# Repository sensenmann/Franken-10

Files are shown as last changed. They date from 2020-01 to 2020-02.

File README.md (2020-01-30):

# Franken-10
**A CR-10 Dual-X-Carriage Mod**

This is my first public Open Source project, so please be kind with me. Also, english isn't my native language - please forgive me typos and grammatical mistakes :wink:

:bangbang::bangbang:
**This is an unstable work in progress!! Don't use it now, until you're willing to contribute to this project!!**
:bangbang::bangbang:

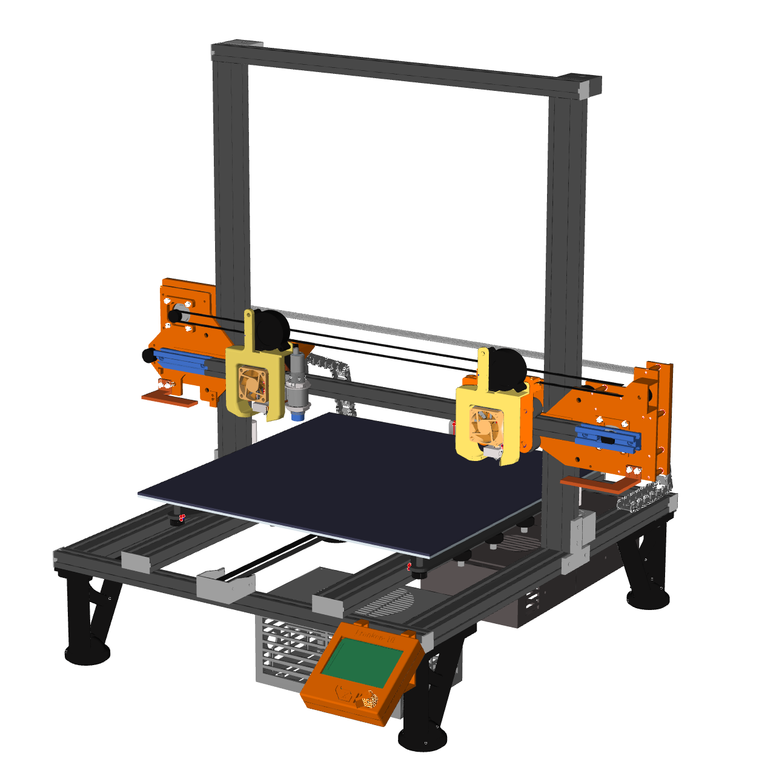
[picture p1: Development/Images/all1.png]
Franken-10


<h3>Table of Contents</h3>
<!-- TOC depthFrom:2 depthTo:6 withLinks:1 updateOnSave:1 orderedList:0 -->

- [Intention](#intention)
- [Benefits](#benefits)
- [Needed parts](#needed-parts)
- [Instructions](#instructions)
- [Firmware](#firmware)
- [FAQ](#faq)

<!-- /TOC -->

## Intention
I wanted to upgrade my awesome Creality CR-10 3D Printer to make it work with **dual X-Carriage** - but without building it completely up from the ground.
Also I want to keep the upgrades **cheap**, so everyone can easily join this journey.

At the moment, the overall costs for the needed parts is around **190€ - 320€**.

## Benefits
- TMC2130 upgrade
- Silent printing (thanks to TMC2130)
- Sensorless homing on X and Y
- Filament-Runout Sensor (by using existing endstops)
- 32 Bit Mainboard
- 2 independent extruders (fast switching)
- Autobedleveling and Mesh-Correction
- Basing on Marlin Firmware V2.0.1
- Using existing CR-10 Frame (no drilling, etc.)

## Needed parts
All needed and optionals parts can be found [here](Parts.md)

## Instructions
Do the CR-10 dual-z upgrade as instructed [here](https://www.sainsmart.com/blogs/news/how-to-install-dual-z-axis-to-upgrade-your-creality-cr-10-3d-printer).  
Skip the controlbox-steps and go directly to the step **Bracket installing**, as we have our own mainboard.

All other steps are documented in the **[manual](Docs)**  
:heavy_exclamation_mark: UNDER CONSTRUCTION :heavy_exclamation_mark:

## Firmware
You can find my fork of Marlin 2.0 [here](https://github.com/sensenmann/Franken-10-Marlin)   
The latest Firmware can be found in the **[releases](../../releases)**-section

## FAQ
Please also read the [FAQ](FAQ.md) - or ask questions by opening an Issue.

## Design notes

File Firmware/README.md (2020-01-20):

# Firmware Update Instructions

- Copy **firmware.bin** to the root of your MicroSD-Card
- Reset your SKR PRO board and wait till the update progress has finished

For further details look at the [original instructions](../../../blob/develop/Docs/3rd-Party/SKR%20PRO%20V1.1%20user%20manual%20v1.1.pdf).

# Build Marlin Firmware

To build the Marlin-Firmware please checkout [my fork](https://github.com/sensenmann/Franken-10-Marlin) of the original Marin-Firmware `bugfix-2.0.x`.

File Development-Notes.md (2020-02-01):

# Development-Notes
## 3D Models
All parts are designed in Fusion360 and located in the git-repository.  
I'm quiet new to Fusion360, so some models are maybe constructed a little bit "strange" in the eyes of experts 😅

At the moment, sensorless homing with `DUAL_X_CARRIAGE`enabled in Marlin wasn't possible for me, so I've had to make an workaround. You can find this fix in my commit **[150d5a9](https://github.com/sensenmann/Franken-10-Marlin/commit/150d5a96bf3c44fadcd32eb3756d982cddc0c70e)**.

I hope someone can help me to fix this workaround.

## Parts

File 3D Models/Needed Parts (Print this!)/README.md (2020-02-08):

# 3D Printing instructions

All parts are mechanical parts and should be printed in the **final version** with ABS/PETG and 100% infill.

For **developing/testing purpose** I've made very good experiences with PLA and 20% infill. This is stable enough! :grimacing:

## Franken-10 Parts

All parts can be printed without supports.  

### X-Holder Parts
- `X-Holder Left - Front.stl`
- `X-Holder Left - Back.stl`
- `X-Rails Extension - Left.stl`
- `X-Holder Right - Front.stl`
- `X-Holder Right - Back.stl`
- `X-Rails Extension - Right.stl`
- `Nozzle Wipe - Left.stl`
- `Nozzle Wipe - Right.stl`
- `M8 Rod Mount Left.stl`
- `M8 Rod Mount Right.stl`
- **18x** `Spacer.stl`
- `Endstopp-Part.stl` *(optional - only need, when you don't have an ABL-Probe)*

### Hotend Carriages
#### for E3D V6 Hotend - recommended
- `Carriage Left - E3DV6.stl`
- `Carriage Left - E3DV6 - Part 2.stl`
- `Carriage Left - E3DV6 - Part 2 - Cap.stl`
- `Carriage Right - E3DV6.stl`
- `Carriage Right - E3DV6 - Part 2.stl`
- `Carriage Right - E3DV6 - Part 2 - Cap.stl`
- `Carriage Right - E3DV6 - Part 2 - ABL.stl`
- **4x** `Nut-Holder.stl`
- **3x** `Exccentric Spacer.stl`

<div style="color: #BBBBBB">

#### for stock hotend *(not updated aynmore)*
- `Carriage Left - Stock Hotend.stl`
- `Carriage Left - Stock Hotend - Part 2.stl`
- `Carriage Left - Stock Hotend - Part 2 - Cap.stl`
- `Carriage Left - Stock Hotend - ABL.stl`
- `Carriage Right - Stock Hotend.stl`
- **3x** `Exccentric Spacer.stl`
</div>

### PSU + Mainboard Enclosures
- `PSU-Enclosure 1.stl`
- `PSU-Enclosure 2.stl`
- `PSU-Enclosure Cover 1.stl`
- `PSU-Enclosure Cover 2.stl`
- `SKR-Enclosure Bottom.stl`
- `SKR-Enclosure Cover.stl`
- `SKR-Enclosure Fan-Cover.stl`
- `SKR-Enclosure Walls.stl`

## 3rd Party Parts
### 5015 Bullseye Fans
Original part from https://www.thingiverse.com/thing:2759439
#### for E3D V6 Hotend - recommended
- **2x** `CR10_E3DV6_MANUAL_BASE_V7.5.stl`
- **2x** `E3DV6_DUCT_V7.5.stl`
- **2x** `E3DV6_OR_VOLC_40MM_CAP_V7.5.stl`

<div style="color: #BBBBBB">

#### for stock hotend *(not updated aynmore)*
- 2x `CR10_STOCK_MANUAL_BASE_V11.3.stl`
- 2x `CR10TEVO_5015_DUCT_V7.5....stl`
- Optional (for Autobed-Leveling):
  - `ALL_18MM_EZABL_X+48_Y-2_RIGHT_V7.5 - mirrored.stl` *(for 18mm Probes)*
  - `ALL_13MM_EZABL_X+48_Y-2_RIGHT_7.5..stl` *(for 13mm Probes)*
</div>

### CR-10 Feet
Original part from https://www.thingiverse.com/thing:3093788  
Print 4x `Pied-CR10-Update.STL` and mount it to the CR-10 frame.

## Filament-Runoutsensor Mount
Original part from http://www.thingiverse.com/thing:3352422  
Print 2x `Filament_Sensor_Crealityv1.stl`  
This part is using your existing CR-10 endstops.

### CR-10 Dual_Z Pulley-Setup
Original part from https://www.thingiverse.com/thing:2628377  
Print `Idle_Pulley_Tension_Bracket.stl`

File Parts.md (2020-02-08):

# Parts
## Needed Parts

| Pic | Name | Shoplink | Price (ca) |
|--|--|--|--|
|  | **CR-10 Dual Z Axis upgrade** | [Amazon](https://amzn.to/2GDkn1D) / [Aliexpress](https://www.aliexpress.com/item/33005235559.html)| 22€ - 45€  |
|  | **SKR Pro v1.1 Mainboard**<br>with 6 Steppermotor-Drivers | [Amazon](https://www.amazon.de/gp/product/B07W5XS572/) / [Aliexpress](https://www.aliexpress.com/item/33042699158.html) | 33€ - 50€ |
|  | **6x TMC2130 Steppermotor Drivers**<br>in SPI-Mode | [Amazon](https://amzn.to/3aTRr3j) / [Aliexpress](https://www.aliexpress.com/item/32907648703.html) | 50€ - 70€ |
|  | **RepRap Discount LCD 12864**<br>with SD-Card Slot | [Amazon](https://amzn.to/37FaMn7) / [Aliexpress](https://www.aliexpress.com/item/4000331136499.html) | 11€ - 16€ |
|  | **6x TMC2130 Steppermotor Drivers**<br>in SPI-Mode | [Amazon](https://amzn.to/2OblObL) / [Aliexpress](https://www.aliexpress.com/item/32907648703.html) | 50€ - 70€ |
|  | **2x Nema 17 Steppermotors**<br>for Extruder & 2nd X-Axis | [Amazon](https://amzn.to/2RZeJfL) / [Aliexpress](https://www.aliexpress.com/item/4000130492082.html) | 10€ - 25€ |
|  | **MK8 Hotend**<br>12 Volt (with PTFE-Tube) | [Amazon](https://amzn.to/2Oc3kYZ) / [Aliexpress](https://www.aliexpress.com/item/4000219883438.html)| 10€ - 25€ |
|  | **2x Metal Bowden Extruder**<br>1 for existing and 1 for new extruder | [Amazon](https://amzn.to/2U7rlUz) / [Aliexpress](https://www.aliexpress.com/item/32834380573.html) | 8€ - 13€ |
|  | **2x 5015 Part Cooling Fans**<br>12 Volt | [Amazon](https://amzn.to/2RE35Yz) / [Aliexpress](https://www.aliexpress.com/item/4000141395273.html) | 2€ - 9€ |
|  | **2x Noctua NF-A4x10 FL**<br>12 Volt - Hotend Fans| [Amazon](https://amzn.to/37I0RwX) | 26€ |
|  | **120mm Fan**<br>12 Volt - for Mainboard | [Amazon](https://amzn.to/2RFA4fl) | 4€ |
|  | **Kepton-Tape + insulating material** | [Amazon](hhttps://amzn.to/38Sxpog) / [Aliexpress](https://www.aliexpress.com/item/4000389787844.html)| 3€ - 9€ |
|  | **4x V-Slot wheels**| [Amazon](https://amzn.to/38S18gS) / [Aliexpress](https://www.aliexpress.com/item/4000234983430.html) | 6€ - 14€ |
|  | **M8 Threaded rod and 2 nuts**| [Obi](https://www.obi.at/gewindestangen/lux-gewindestangen-m8-x-1-000-mm-verzinkt/p/7608896) | 2€ |
|  | **GT2 Timing-Belt Set**| [Amazon](https://amzn.to/37GUvxM) / [Aliexpress](https://www.aliexpress.com/item/4000091123800.html) | 4€ - 16€ |
|||**Sum**| **190€ - 320€**|

## Recommended Parts
| Pic | Name | Shoplink | Price (ca) |
|--|--|--|--|
|  | **2x E3D V6 Hotend** *(or clone)* <br> An absolute must-have for printing fast | [Amazon](https://amzn.to/2H8Hl0S)| 12€  |

## Assembly-Material ##
| Pic | Name | Shoplink | Price (ca) |
|--|--|--|--|
  | **M3 Screws- and Nuts-Set** | [Amazon](https://amzn.to/2RFuKIG) | 15 € |
|  | **Stepper-Motor Cables** | [Amazon](https://amzn.to/37I12s7) | 10€ |
|  | **Crimp-Set** | [Amazon](https://amzn.to/2ta2J2u) | 19€ |

## Optional Parts
| Pic | Name | Shoplink | Price (ca) |
|--|--|--|--|
|  | **Inductive Sensor for auto bedleveling** <br> Depends on the distance from nozzle to the steelbed <br> :heavy_exclamation_mark:THIS SENSORS ONLY DETECTS METAL:heavy_exclamation_mark: <br> You need to have a steel buildplate| [Amazon (8mm distance)](https://amzn.to/36C1DKr)<br>or<br>[Amazon  (4mm distance)](https://amzn.to/2vztpdX)| 8€  |
| <br> | **GT2 Timing Pulley and Belt (852mm)**<br>for syncing the 2 Z-Axis | [Amazon](https://amzn.to/2REfkEr) and [Amazon](https://amzn.to/31882fB) | 17€  |
| | **Flexible Cord Organizer**<br>for cable-management | [Amazon](https://amzn.to/2vCcS9f) | 9€ |

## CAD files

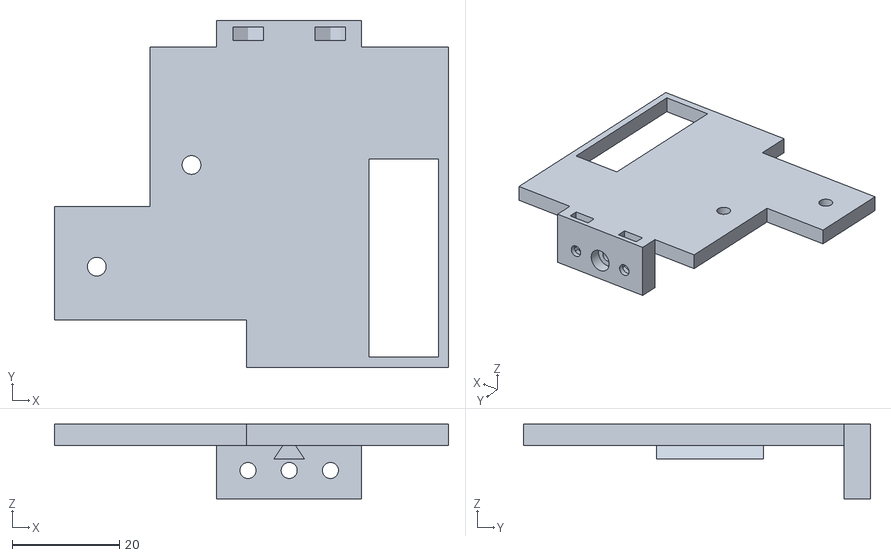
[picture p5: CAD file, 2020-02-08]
3D Models/Needed Parts (Print this!)/Franken-10/Carriage-Left E3DV6 - Part 2.stl
73.6 x 64.8 x 13.9

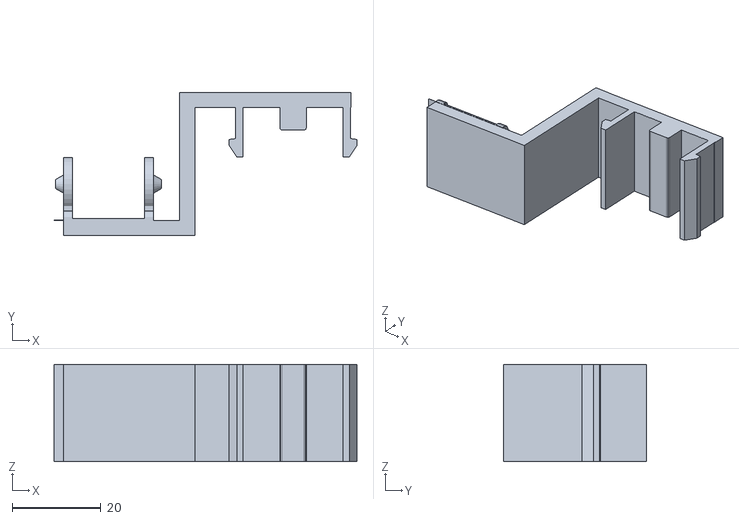
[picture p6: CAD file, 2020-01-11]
3D Models/Optional Parts/3rd Party Parts/cablchain-heatedbed.stl
68.4 x 32.4 x 22.0

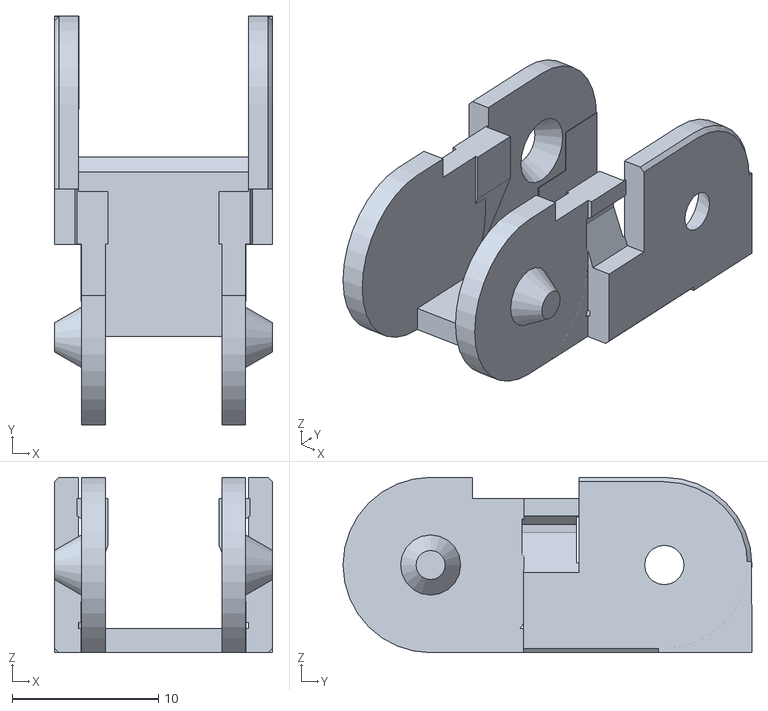
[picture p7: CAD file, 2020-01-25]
3D Models/Optional Parts/3rd Party Parts/Ender_3_Cable_Chain_/files/cableChain_link_v3 - small v2.stl
14.9 x 28.0 x 12.0

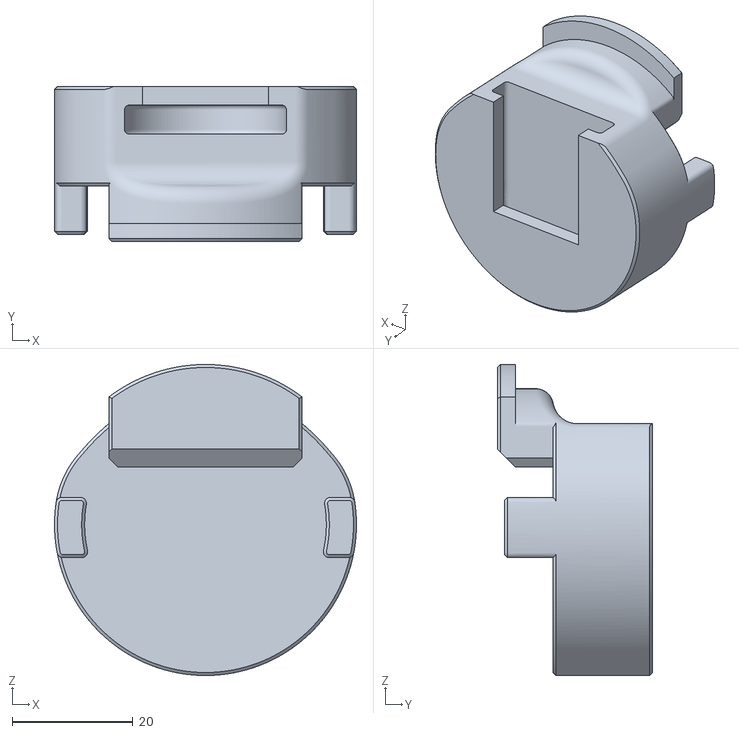
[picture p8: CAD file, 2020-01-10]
3D Models/Optional Parts/3rd Party Parts/Filler_-_The_Customizable_Filament_Holder_that_fills_your_printer_/files/FillerBraceUltimaker.stl
50.0 x 25.7 x 51.5

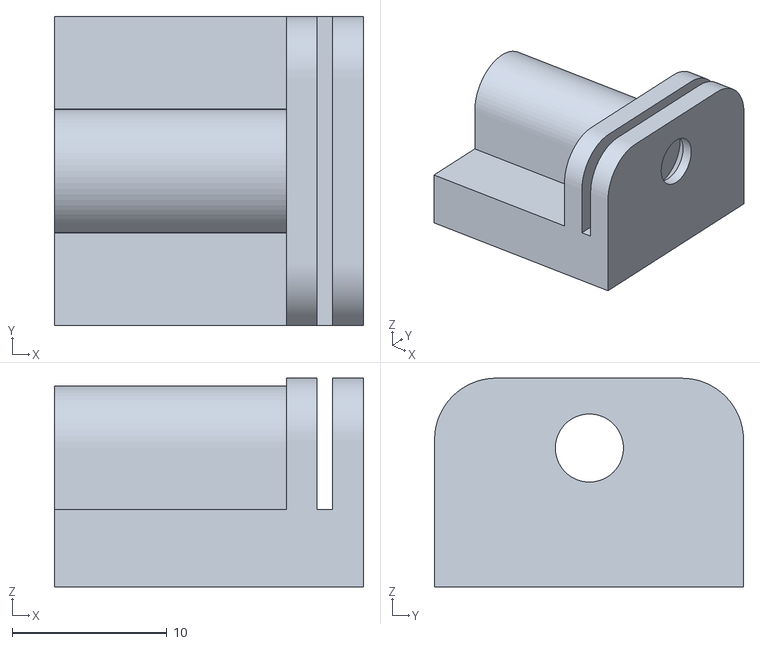
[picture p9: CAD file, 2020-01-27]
3D Models/Optional Parts/3rd Party Parts/PTFE_Tube_Cutting_Guide/files/PTFE_tube_cutting_guide.stl
20.0 x 20.0 x 13.5

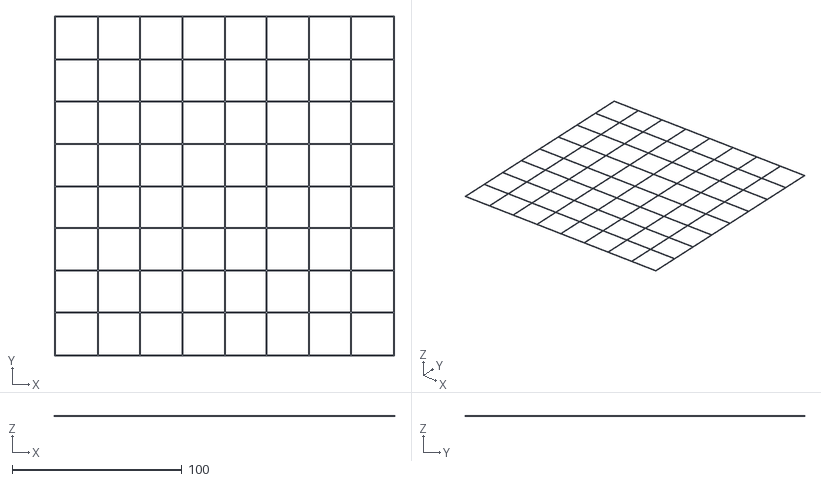
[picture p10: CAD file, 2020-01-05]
3D Models/Optional Parts/Test-Prints/Anet_A8_bed_level_test/files/Bed_calibration_test.stl
200.0 x 200.0 x 0.2

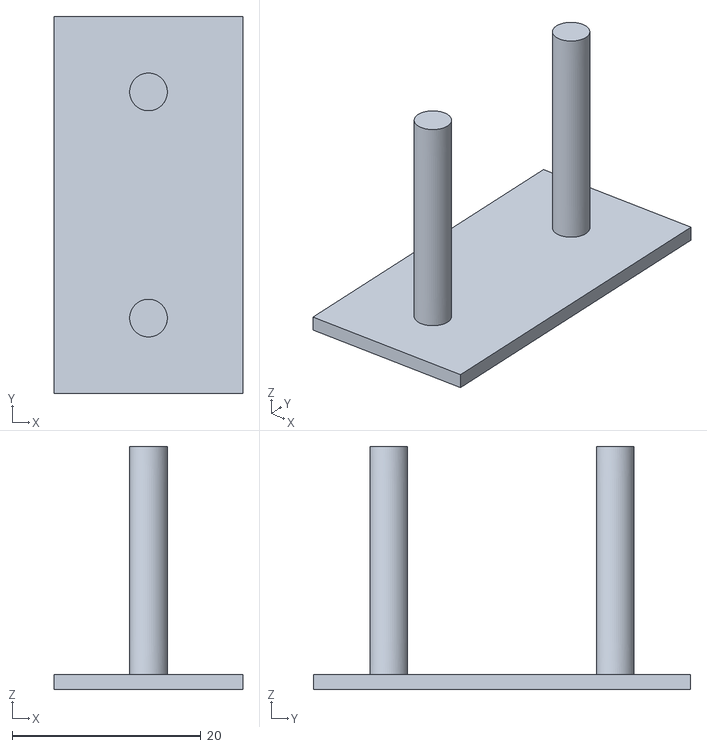
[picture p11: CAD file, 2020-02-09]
3D Models/Optional Parts/Test-Prints/Basic_Stringing_Test/files/Stringing_Test.stl
20.0 x 40.0 x 25.8

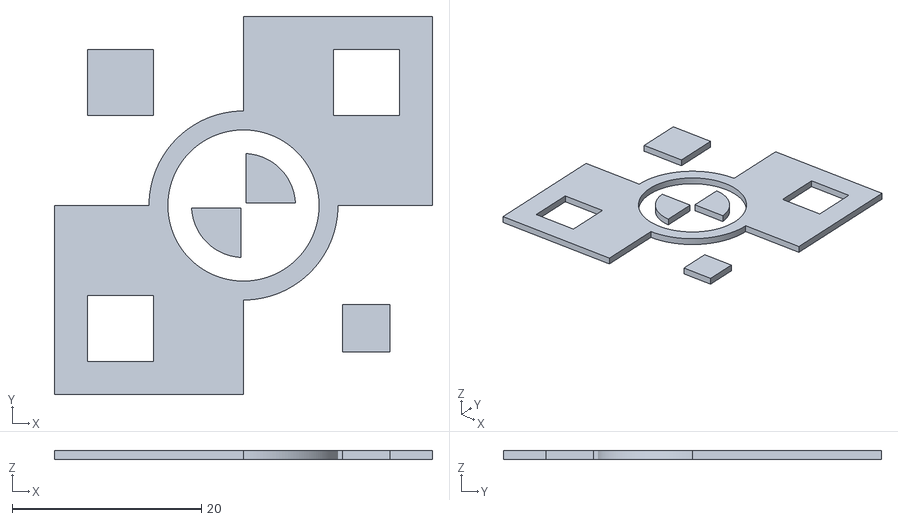
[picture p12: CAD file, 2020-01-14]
3D Models/Optional Parts/Test-Prints/Dual_Extruder_Calibration_Print/Dual_Extruder_Calibration_Print8f583c7d6bd55e315dafb2d913d98688-Calibration_Target_B_v1-1.STL
40.0 x 40.0 x 1.00

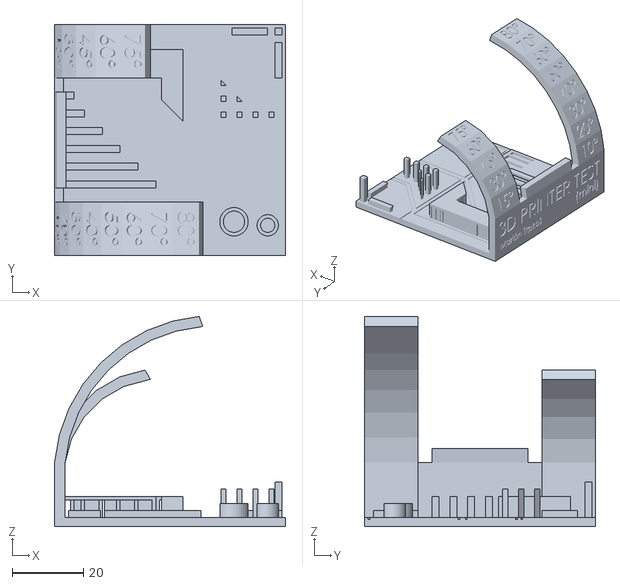
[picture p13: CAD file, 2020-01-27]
3D Models/Optional Parts/Test-Prints/MINI_All_In_One_3D_printer_test/files/3D_printer_test_mini_-_no_text.STL
65.0 x 65.0 x 59.1

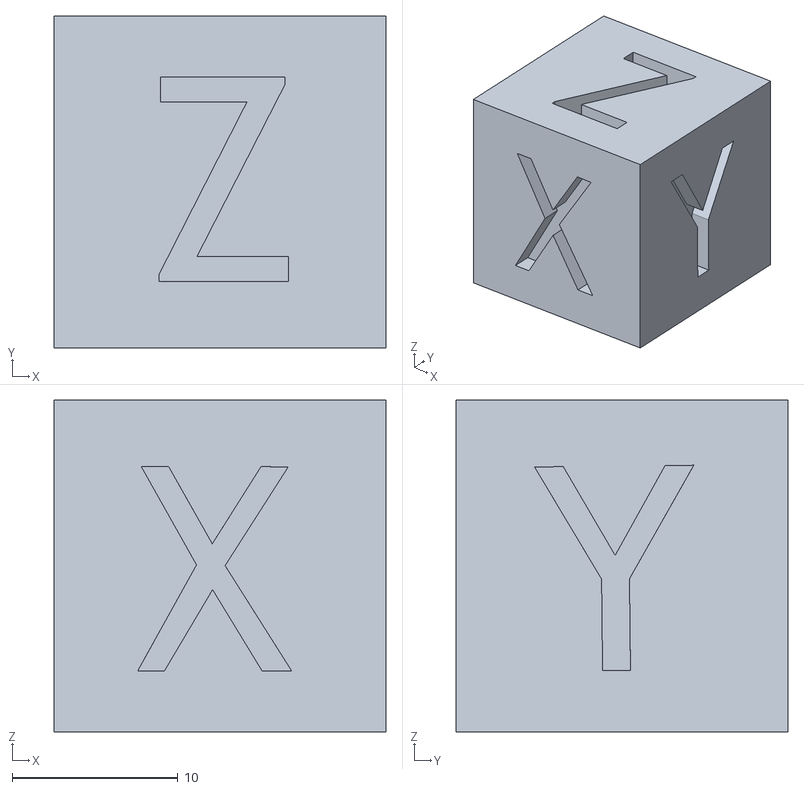
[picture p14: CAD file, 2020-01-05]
3D Models/Optional Parts/Test-Prints/XYZ_20mm_Calibration_Cube/files/xyzCalibration_cube.stl
20.0 x 20.0 x 20.0

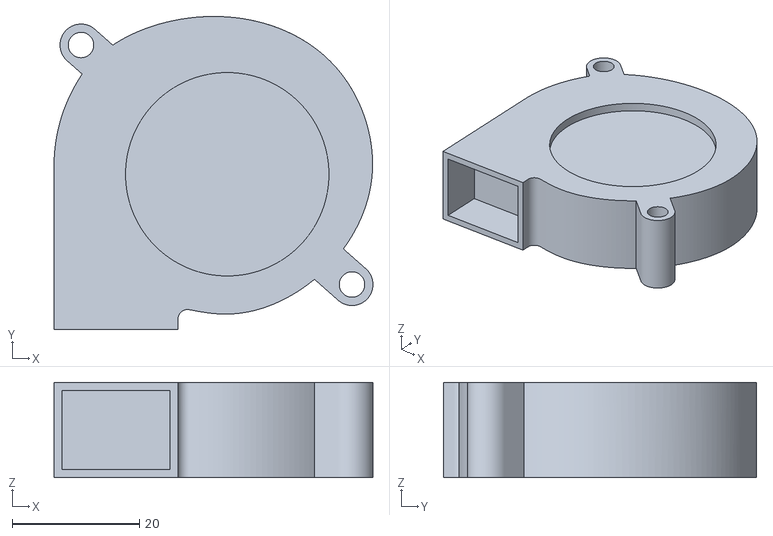
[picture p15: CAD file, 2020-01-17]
Development/3D Models/Models for 3D Design/5015_Blower_Fan_50x15/files/5015_Blower_Fan.stl
50.2 x 49.2 x 15.0

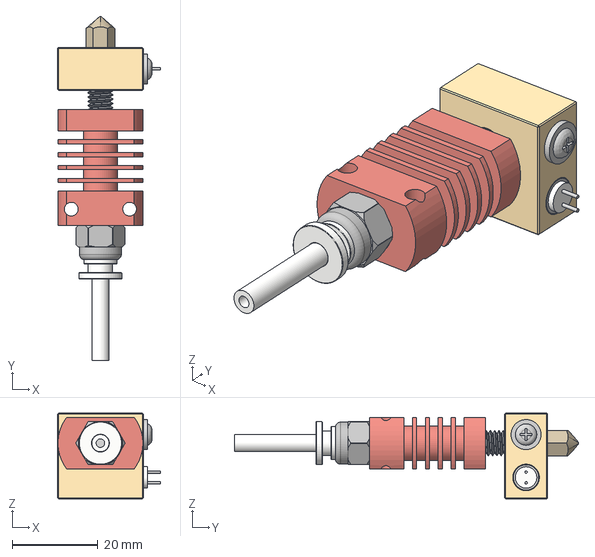
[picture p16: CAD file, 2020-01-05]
Development/3D Models/Models for 3D Design/creality-cr-10-hotend-1/cr10hotend v14.step
24.0 x 80.2 x 20.0 mm

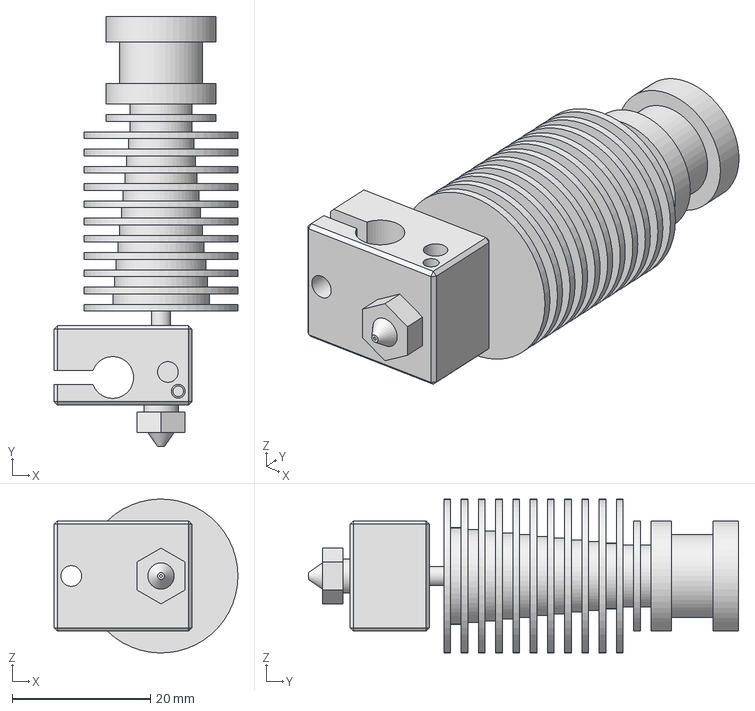
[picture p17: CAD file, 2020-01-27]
Development/3D Models/Models for 3D Design/E3D_V6_HotEnd_CAD_Models_Includes_all_3_versions/E3D_V6_1.75mm_Universal_HotEnd_Mockup.stp
26.7 x 62.3 x 22.3 mm

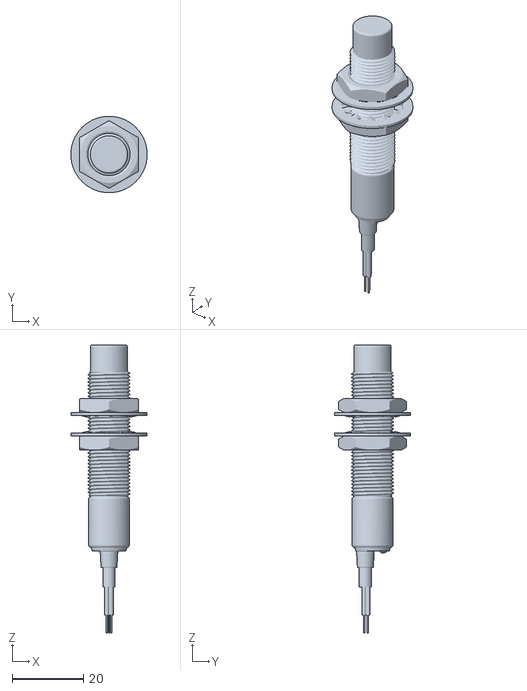
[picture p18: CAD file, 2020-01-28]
Development/3D Models/Models for 3D Design/Inductive-Sensor.stl
21.5 x 21.5 x 81.0

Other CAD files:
Development/3D Models/Models for 3D Design/mk8-direct-drive-extruder-7mm-pulley-adapter/adapter_left_closed.stl
Development/3D Models/Models for 3D Design/Nema17+Stepper+Motor+Model/files/Nema17_v6.stl
Development/3D Models/Models for 3D Design/Nema17+Stepper+Motor+Model/images/tiny_thumb_Nema17_v6.stl
Development/3D Models/Models for 3D Design/Tevo_Tarantula_Stock_extruder_with_e3d_bowden_coupler_adapter/files/ExtruderBottom_v1.stl
3D Models/Optional Parts/3rd Party Parts/PTFE_Tube_Cutting_Guide/files/ptfe_cutting_guide.scad
3D Models/Needed Parts (Print this!)/Franken-10/Carraige Left - E3DV6.stl
3D Models/Needed Parts (Print this!)/Franken-10/Carriage Left - Stock Hotend - ABL.stl
3D Models/Needed Parts (Print this!)/Franken-10/Carriage Left - Stock Hotend - Part 2 - Cap.stl
3D Models/Needed Parts (Print this!)/Franken-10/Carriage Left - Stock Hotend - Part 2.stl
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

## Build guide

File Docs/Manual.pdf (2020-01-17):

## CR-10 at it’s max!

# Franken-10

A CR-10 Dual Extruder Mod

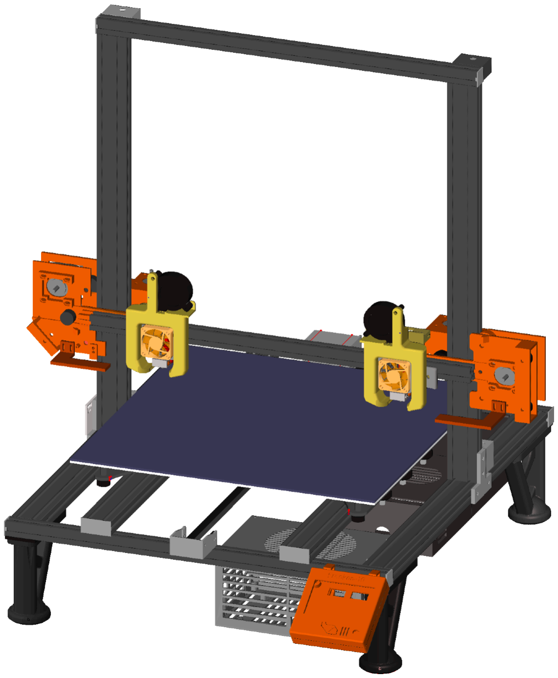
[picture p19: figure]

## Index

Introduction | 3
About the author | 4
Changed / Updated Parts | 5
Untouched Parts | 9
Parts we don’t need anymore | 9
Preparations | 10

## Introduction Intention

I wanted to upgrade my awesome Creality CR-10 3D Printer to make it work with dual axis -but without building it completely up from the ground. Also I want to keep the upgrades cheap, so everyone can easily join this journey.

## Benefits

- Using existing CR-10 Frame (no drilling, etc.)
- TMC2130 upgrade
- Silent printing (thanks to TMC2130)
- Sensorless homing on X and Y
- Filament-Runout Sensor (using existing endstops)
- 32 Bit Mainboard
- 2 independent extruders (fast switching, no purge-block)
- Auto bed-leveling and Mesh-Correction
- basing on newest Marlin Firmware (V2.1.x)

## Sources

All sources can be found on GitHub:

- Franken-10 related stuff: https://github.com/sensenmann/Franken-10
- Github fork: https://github.com/sensenmann/Franken-10-Marlin

## About the author

I’m a Software Developer, located in Vienna / Austria. In the year 2018 I’ve started 3D printing, and the CR-10 was my first 3D printer. After learning a lot about 3D printers, I’ve also bought an Ender 3 and a Prusa i3 MK3S (later with MMU2S).

My CR-10 has en enormous buildplate, but was it was lacking a lot of features of the Prusa i3, so I didn’t use it anymore for a long time.

Mid 2019 I’ve started to start the Franken-10 project, because I wanted to use my CR-10 again - with all the nice features of the Prusa i3.

English isn’t my native language, so please be kind if there are some typos.

## Changed / Updated Parts Mainboard

The stock CR-10 mainboard get’s replaced with the BigTreeTech SKR Pro, which supports 6 stepper motors.

•X1 (Left Extruder)
•X2 (Right Extruder)
•Y-Axis
•Z-Axis (2 plugs for 2 z-axis motors) •E1 (Left Extruder)
•E2 (Right Extruder)

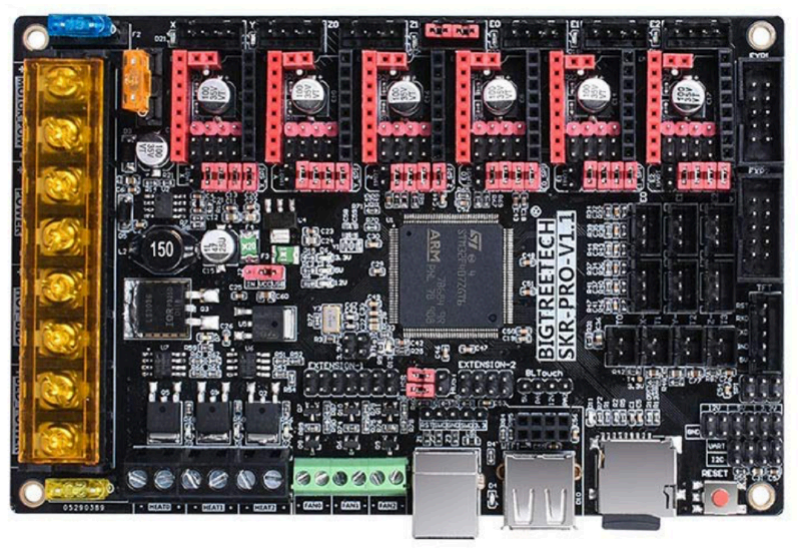
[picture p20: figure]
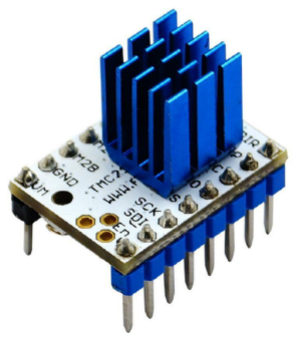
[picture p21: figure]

## Stepper Motor Drivers

We update to TMC2130 stepper-motor drivers to get quiet and reliable prints.

The TMC2130 also allows sensorless homing on X and Y axis, so we can reuse the stock-endstops as filament sensors.

## LCD-Display with SD-Card Slot

Unfortunately we can’t use the Micro-SD-Card Slot of the SKR-Mainboard, so we need a new LCD Display with integrated
SD-Card Slot.

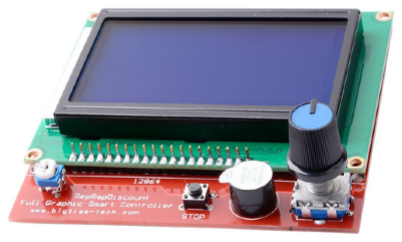
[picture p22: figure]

The good news: We now can use big SD-Cards instead of the tiny Micro-SD-Cards.

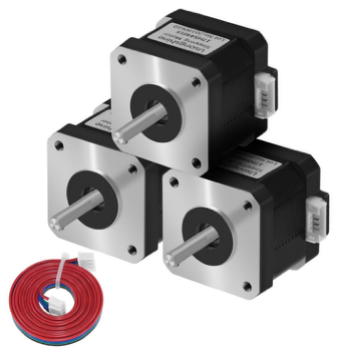
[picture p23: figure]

## Additional Stepper Motors

We need 2 additional stepper-motors. One motor for the 2nd hotend on the x-axis and one motor as the extruder for this new hotend.

## 2nd Hotend

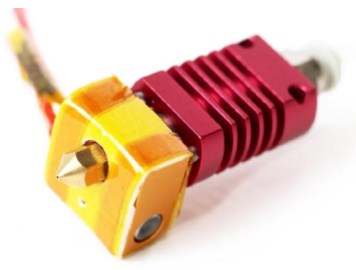
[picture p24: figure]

Of course we need a second Hotend for our dual hotend setup. I’ve chosen the same hotend, as the CR-10 already uses (MK8). An upgrade to E3D Volcano is not part of this instruction at the moment, but is of course possible.

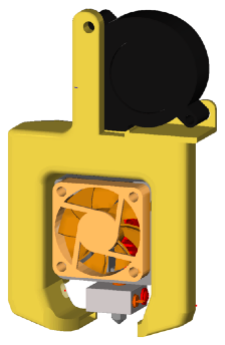
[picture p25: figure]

## Petsfang-Cooler and 5015 fans

For optimal cooling we upgrade our Hotends to Petsfang-Cooler with 5015 fans and Noctua 40x40x10 fans.

Original part from https://www.thingiverse.com/thing:2759439

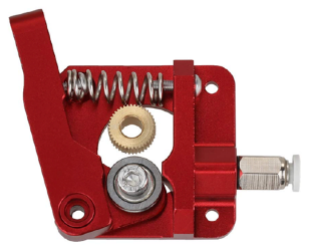
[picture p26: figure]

## Aluminium Bowden Extruder

I’ve always hated the stock CR-10 plastic extruder, so I’m upgrading to all metal extruders. We need of course two of this.

Tip: Buy one left- and one right-handed.

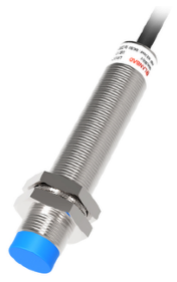
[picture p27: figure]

## Auto Bed-Leveling with inductive Sensor

For Homing the Z-Axis and for leveling the bed, I’m using an inductive sensor. This sensor only detects metal, so you need one, which can measure far enough to detect your steelbed - or use an metallic build plate (which I recommend).

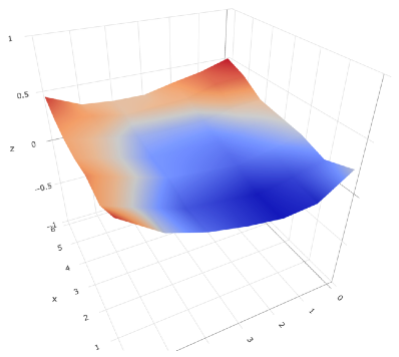
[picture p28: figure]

The firmware takes a lot of measuring-points and generate a mesh of your print bed.

This mesh will be reconsidered while printing, so you don’t have to level your bed again.

Also uneven build-plates are no problem anymore.

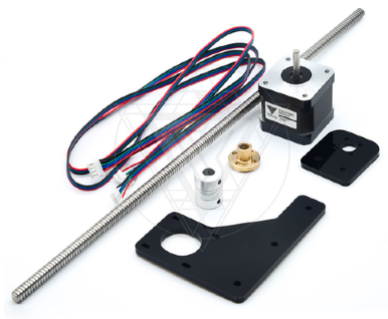
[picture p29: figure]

## Dual Z-Axis Upgrade

With our modifications we generate a lot of weight on our Z-Axis. So I recommend upgrading to a dual z-axis setup.

The 2nd z-motor can easily plugged in into the SKR Pro mainboard.

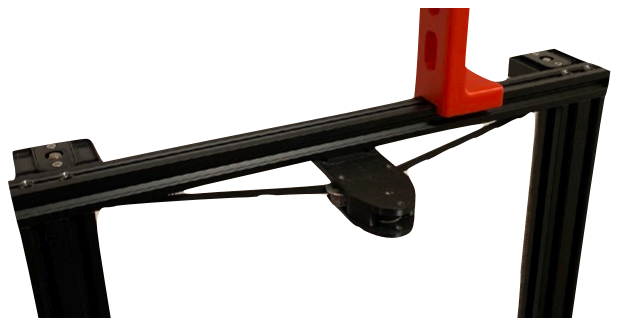
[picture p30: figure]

For perfect results, we use a timing belt to
sync these two Z-rods.

## Control-Box

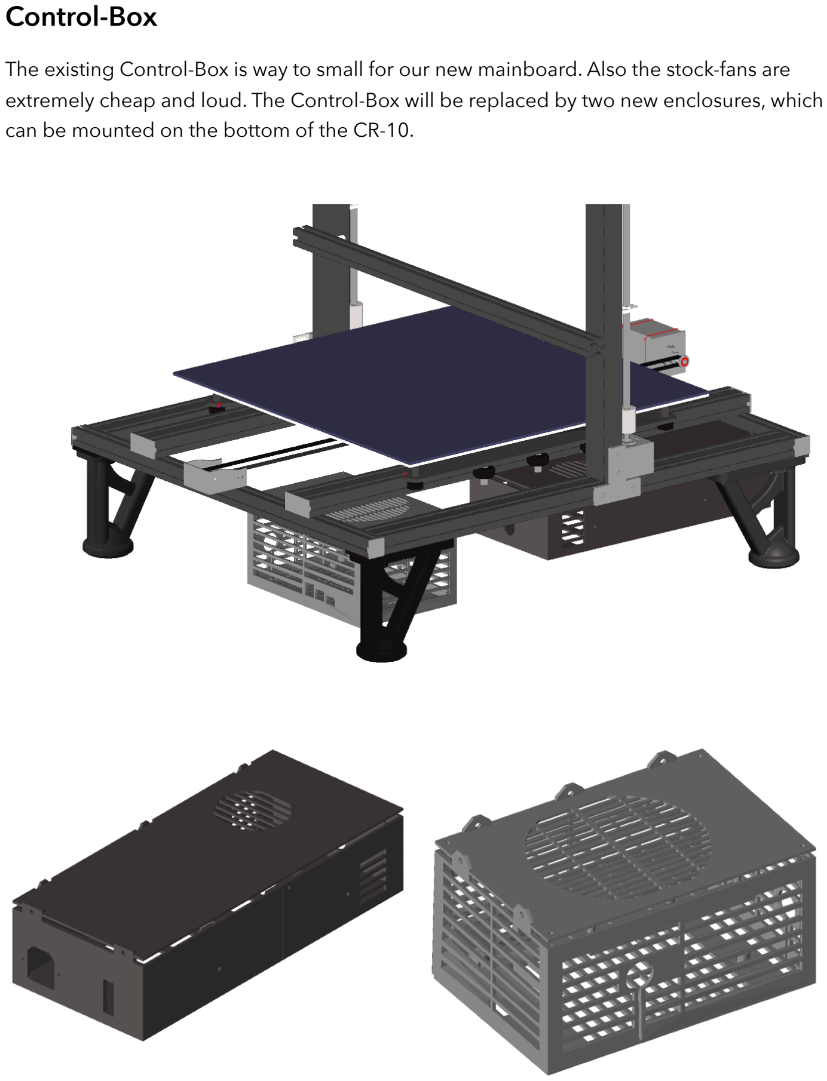
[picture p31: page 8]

The existing Control-Box is way to small for our new mainboard. Also the stock-fans are extremely cheap and loud. The Control-Box will be replaced by two new enclosures, which can be mounted on the bottom of the CR-10.

## Untouched Parts

This parts do not be changed or modified:

- PSU
- Heated Bed
- The whole CR-10 Frame

## Parts we don’t need anymore

The following parts aren’t needed anymore, because they are upgraded / replaced:

- Stock Display (we need a LCD with SD-Card-Slot)
- Control-Box (we need more space for our board)
- Stock-Fan
- Extruder-Carriage
- Stock Timing-Belt (we need two longer ones)

## Preparations Buy the needed parts

Buy all the parts, listed on the GitHub page: https://github.com/sensenmann/Franken-10#needed-parts

## Print the needed parts

3D print all the parts listed on the GitHub page:

https://github.com/sensenmann/Franken-10/tree/master/3D%20Models/Needed%20Parts%20(Print%20this!) (https://github.com/sensenmann/Franken-10/tree/master/3D%20Models/Needed%20Parts%20(Print%20this!))

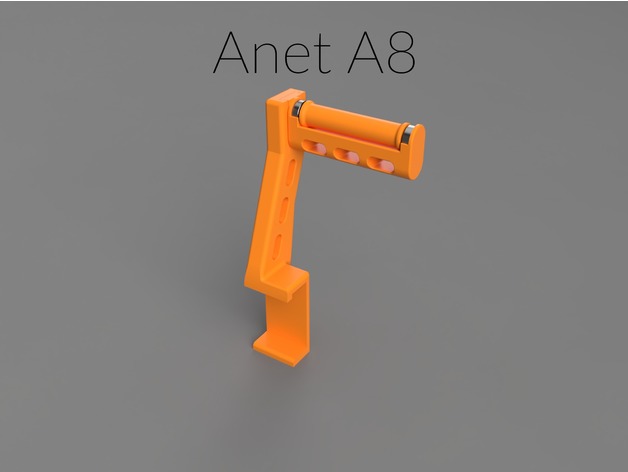
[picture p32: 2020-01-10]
3D Models/Optional Parts/3rd Party Parts/Filler_-_The_Customizable_Filament_Holder_that_fills_your_printer_/images/794fcd875c39b02076b46ccfd99a0f10_preview_featured.jpg

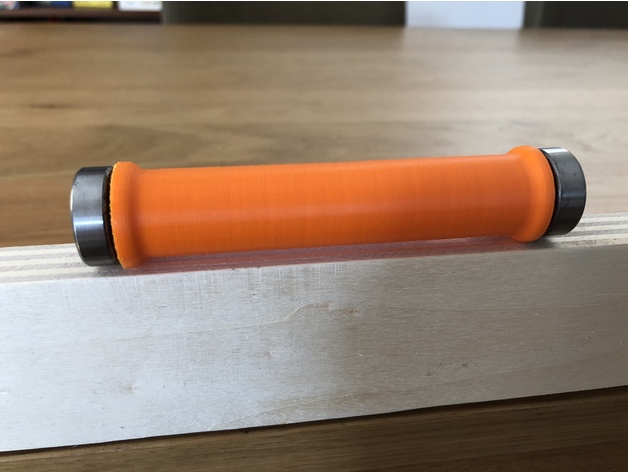
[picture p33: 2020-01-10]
3D Models/Optional Parts/3rd Party Parts/Filler_-_The_Customizable_Filament_Holder_that_fills_your_printer_/images/ced1312db36f0a4b0895dd92cab77ae7_preview_featured.jpg

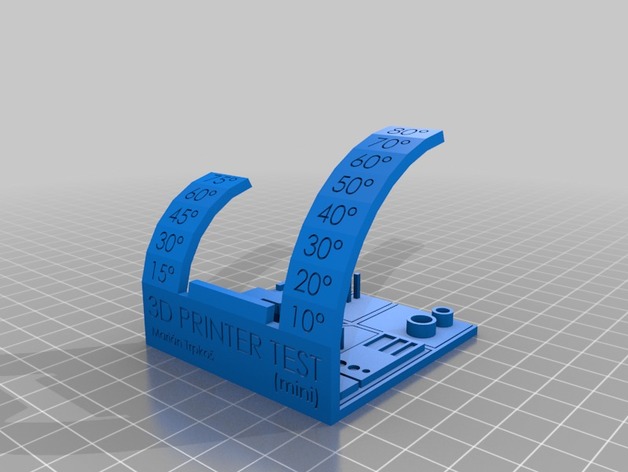
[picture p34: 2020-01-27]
3D Models/Optional Parts/Test-Prints/MINI_All_In_One_3D_printer_test/images/d589e523e2310a4dbcdbe5f741e632cd_preview_featured.jpg

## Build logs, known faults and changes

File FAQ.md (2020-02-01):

# FAQ

<!-- TOC depthFrom:2 depthTo:6 withLinks:1 updateOnSave:1 orderedList:0 -->

- [General](#general)
	- [How big is the build-volume?](#how-big-is-the-build-volume)
	- [What modes are supported?](#what-modes-are-supported)
	- [Why still using 12V PSU?](#why-still-using-12v-psu)
	- [What skills to I need to perform this?](#what-skills-to-i-need-to-perform-this)
	- [Is it safe?](#is-it-safe)
	- [Which slicer can I use?](#which-slicer-can-i-use)

<!-- /TOC -->
## General
### How big is the build-volume?
The Franken-10 extends the existing X-rail, where the hotends travel on both sides, so there is additional space for the inactive extruder to park.
This is made to keep the build-volume as big as possible.  
- Single-Extrusion: 300x300x400mm
- Dual-Extrusion: 280x300x400mm
- Duplicate-Mode: 150x300x400mm *(your model can only use the half width)*

### What modes are supported?
You can still print in single extrusion mode, with your existing slicer and profiles.
If you want to print with two filaments, there are this options:
- Single-Extrusion
- Dual-Extrusion (two colors or two filament-types)
- Duplicate-Mode (the same model printed at the same time)

### Why still using 12V PSU?
Of course, 24V would heat up the extruder(s) and the bed a little bit quicker, but this would lead to additional costs (PSU and 24V-Heated Bed).
If you want to do this upgrade, you can do this. The SKR PRO-Board supports Voltages from 12V - 24V without modifications.

### What skills to I need to perform this?
There are **no programming skills** needed. Although, you need to completely disassemble your control-box and **soldier** a few cables.
Also you need to print the parts yourself on your printer.  
You don't need to drill anything in your existing CR-10 Frame or something like this.

### Is it safe?
The Firmware is based on Marlin 2.0.x with Thermal Runaway Protection enabled.

### Which slicer can I use?
You can use any slicer that supports two extruders.
Franken-10 comes with preconfigured **PrusaSlicer-Profiles**, which I recommend.

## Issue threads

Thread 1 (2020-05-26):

Firmware

Kiyotimun, 2020-05-26:
I have the same motherboard and was looking at your VS code. First question is does it work? I don't have a sensor mounted yet nor do I want filament run-out yet. Something stuck out that you have E2 and X2 activated in the Stepper Driver area of config.h. I would be willing to help with this since no one else has tried this but us two (lol).

/**
 * Stepper Drivers
 *
 * These settings allow Marlin to tune stepper driver timing and enable advanced options for
 * stepper drivers that support them. You may also override timing options in Configuration_adv.h.
 *
 * A4988 is assumed for unspecified drivers.
 *
 * Options: A4988, A5984, DRV8825, LV8729, L6470, L6474, POWERSTEP01,
 *          TB6560, TB6600, TMC2100,
 *          TMC2130, TMC2130_STANDALONE, TMC2160, TMC2160_STANDALONE,
 *          TMC2208, TMC2208_STANDALONE, TMC2209, TMC2209_STANDALONE,
 *          TMC26X,  TMC26X_STANDALONE,  TMC2660, TMC2660_STANDALONE,
 *          TMC5130, TMC5130_STANDALONE, TMC5160, TMC5160_STANDALONE
 * :['A4988', 'A5984', 'DRV8825', 'LV8729', 'L6470', 'L6474', 'POWERSTEP01', 'TB6560', 'TB6600', 'TMC2100', 'TMC2130', 'TMC2130_STANDALONE', 'TMC2160', 'TMC2160_STANDALONE', 'TMC2208', 'TMC2208_STANDALONE', 'TMC2209', 'TMC2209_STANDALONE', 'TMC26X', 'TMC26X_STANDALONE', 'TMC2660', 'TMC2660_STANDALONE', 'TMC5130', 'TMC5130_STANDALONE', 'TMC5160', 'TMC5160_STANDALONE']
 */
#define X_DRIVER_TYPE  TMC2130
#define Y_DRIVER_TYPE  TMC2130
#define Z_DRIVER_TYPE  TMC2130
#define X2_DRIVER_TYPE TMC2130
//#define Y2_DRIVER_TYPE A4988
//#define Z2_DRIVER_TYPE A4988
//#define Z3_DRIVER_TYPE A4988
//#define Z4_DRIVER_TYPE A4988
#define E0_DRIVER_TYPE TMC2130
#define E1_DRIVER_TYPE TMC2130
#define E2_DRIVER_TYPE TMC2130
//#define E3_DRIVER_TYPE A4988
//#define E4_DRIVER_TYPE A4988
//#define E5_DRIVER_TYPE A4988
//#define E6_DRIVER_TYPE A4988
//#define E7_DRIVER_TYPE A4988

sensenmann, 2020-05-31:
Hey! 🙂
Thank you for your feedback 🙂
Yes, the printer works - I'm using it most of the time in duplicate-mode and not multimaterial/multicolor. But my project lacks a lot of documentation ... especially assembly documentation 😅

Maybe we can work together? 🙃
If you send me an email to rene.huber [at] rhse.at, I can share my Whatsapp oder Telegram-Contactinfos with you, for better communication.

Greetings from Austria
René aka Sensenmann

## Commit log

2020-01-05 Renamed Foled
    [18to12.5Topsleeve.stl, 18to12.5bottomsleeve.stl, ABL_TOUCH_MI_DEBIAX_7.23.stl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]
2020-01-05 Franken-10 Parts
    [Endstopp-Part.stl, Extruder Carrier - Left.stl, Extruder Carrier - Right.stl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]
2020-01-05 Added photos of the printer
2020-01-10 Added optional parts
    [3DPNFilHoldBrace.stl, 3DPNFilHoldGuide.stl, 3DPNFilHoldRoller.stl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]
2020-01-11 Added pin layout picture
2020-01-11 Added pin layout picture (as jpeg)
2020-01-11 Added selfmade STLs for Cablechain-Connetcions
    [cablchain-heatedbed.stl, cablechain-connection.stl]
2020-01-11 Updated pin-layout
2020-01-12 Added Filament-Runoutsensor Mounts and updated print-readme
    [Filament_Sensor_Crealityv1.stl]
2020-01-12 Added 120mm fan to readme
2020-01-12 Updated image of printer
2020-01-12 Added T-Nut 2020 (all credits to https://www.thingiverse.com/thing:1609323)
    [T-NUT_M3_3.stl, T-NUT_M3_4.stl]
2020-01-14 Added Calibration-Models
    [Dual_Extruder_Calibration_Print8f583c7d6bd55e315dafb2d913d98688-Calibration_Target_B_v1-1.STL, Dual_Extruder_Calibration_Printc55beef74c122c69c80c3bef6b349fd6-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]
2020-01-15 Udpated Neededparts
    [60T_Pulley_Adapter.stl, Bearing_Spacer.stl, Below_Pulley_Spacer.stl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]
2020-01-16 Added Fusion360 Files
    [Carriage Left.f3d, Carriage Right.f3d, LCD Enclosure.f3d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]
2020-01-17 Updated 3D Models
    [Dual Z-Axis Belt-Tensioner.f3d, Nozzle Wipe - Left.f3d, Nozzle Wipe - Right.f3d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]
2020-01-17 Added Bowden Extruder Model for 3D modeling
    [ExtruderBottom_v1.stl, stockextruderWithE3dCoupler.f3d]
2020-01-17 Added Cable-Chain and plain CR-10 Frame for 3D Modeling
    [cr-10 frame.obj]
2020-01-17 Added 5015-fan and MK8 extruder for 3D modeling
    [5015_Blower_Fan.stl, adapter_left_closed.stl, adapter_left_open.stl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]
2020-01-17 Added assembly-material to readme
2020-01-19 Updated right fan-base
2020-01-19 Updated Homing- and Start-GCodes
2020-01-20 Updated marlin-version in readme
2020-01-21 Updated 3D parts
    [cableChain_linkCover_v2 - small.stl, cableChain_link_v3 - small.stl]
2020-01-24 Updated calibraton-gecodes
2020-01-25 Updated calibration-, homing- and startup-gcodes
2020-01-25 Updated 3D-models
    [LCD-Knob.stl, cableChain_linkCover_v2 - small+long.stl, cableChain_link_v3 - small v2.stl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]
2020-01-27 Added 3d-models für 3d-design
    [E3D_V6_1.75mm_Universal_HotEnd_Mockup.stl, E3D_V6_1.75mm_Universal_HotEnd_Mockup.stp, E3D_V6_3.00mm_Bowden_HotEnd_Mockup.stl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]
2020-01-27 added another testing-model
    [3D_printer_test_mini.STL, 3D_printer_test_mini_-_no_text.STL]
2020-01-27 Added PTFE-Tube Cutter
    [PTFE_tube_cutting_guide.stl, ptfe_cutting_guide.scad]
2020-01-27 Added M8 Thread Rod Mount to 3D Models
    [M8 Rod Mount Left.stl, M8 Thread Mount Right.stl, X-Holder Left - Back.stl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]
2020-01-27 Added Marlin-Statusscreen Images
2020-01-27 Added M8 Threaded Rod to Readme
2020-01-28 Updated Documentation, added buildplate for duplication-printing
2020-01-28 stable Franken-10 firmware V0.1 (basing on Marlin V2.0.1)
2020-01-28 Refactored directory-structure
    [18to12.5Topsleeve.stl, 18to12.5bottomsleeve.stl, 3DPNFilHoldBrace.stl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]
2020-01-29 Changed left Hotend-Carrier from 3 wheels to 4 wheels
    [Carriage Left - Adjustment 1.stl, Carriage Left - Adjustment 2.stl, Carriage Left.stl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]
2020-01-29 Updated GCodes for Calibration (Marlin)
2020-01-29 Added 3D-Models for PSU- and SKR-Enclosure
    [M8 Rod Mount Left.stl, M8 Rod Mount Right.stl, M8 Thread Mount Right.stl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]
2020-02-08 Updated from Stock-Hotend to E3DV6-Hotend (highly recommended)
    [Carraige Left - E3DV6.stl, Carriage Left - Adjustment 1.stl, Carriage Left - Adjustment 2.stl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]
2020-02-08 Updated parts-documentation for E3D V6-Hotend upgrade
2020-02-09 Added Stringing-Test from Thingiverse
    [Stringing_Test.stl]
